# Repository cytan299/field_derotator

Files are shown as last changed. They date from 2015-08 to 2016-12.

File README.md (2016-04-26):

# A Field DeRotator for Alt-Az Mounted Telescopes Used for Astrophotography

by C.Y. Tan 2015

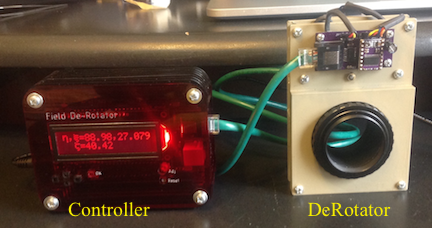
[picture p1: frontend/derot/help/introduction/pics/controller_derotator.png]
Field DeRotator


Most telescopes used for astrophotography are equatorially
mounted. However, the more popular computer controlled telescopes are
alt-az mounted and are usually deemed unsuitable for
astrophotography. The reason is that alt-az mounted telescopes have
one more degree of freedom that is not corrected because it does not
affect visual observations of celestial objects. Unfortunately, by
leaving it uncorrected, alt-az telescopes cannot be used for long
exposure astrophotography. In order to overcome this flaw in alt-az
mounted telescopes, I have designed and built a field derotator that
removes this degree of freedom and thus allows alt-az telescopes to
become astrophotography platforms.

## Goal

I have built a fully functional field derotator that consists of both
a mechanical derotator and an Arduino based controller for the
LX200. All hardware, drawings, schematics, software and documentation
are open source with the respective licenses described below.

I hope that this device will be useful for astrophotographers who find
polar mounts a real pain in the rear to use, and prefer alt-az mounts
instead.

## IMPORTANT!

Field derotation **cannot** work without an off-axis guider. If you
don't plan on investing in an off-axis guider, don't bother building
this device because field derotation will not work without it.  See
[field_derotator_formula.pdf](field_derotator_formula/field_derotator_formula.pdf)
for the explanation.

## MAC OS X Frontend Executable

A compiled app bundle for the Mac can be downloaded from the
[releases repository](https://github.com/cytan299/field_derotator/releases).

## Support

All the software have been successfully compiled on Mac OS X 10.10.5
(Yosemite).

I don't do Windows or Linux so, I cannot answer questions for these
two platforms.

This is unsupported software and hardware. Build at your own peril! :)

You can submit questions or bug reports using the
[issues](https://github.com/cytan299/field_derotator/issues) tab on
the right and then click on **NEW**.

Have fun!

## Directory structure

* **arduino** The C++ code for the arduino MEGA2560.
* **arduino_case** The case design for the field derotator controller.
* **bom** Bill of materials for 1 field derotator. I also show the
  cost for building one.
* **eagle** Eagle schematic and board files.
* **emachineshop** eMachineshop files for the derotator aluminium
shell.
* **field_derotator_formula** derivation of the derotation formula,
  analysis of how off-axis guiding is improved with derotation and
  limitation of derotation.
* **frontend** C++ code for the GUI frontend for the user to control
the derotator.
* **howto** Guides for how to assemble the derotator and the
controller.

## Other information

More information can be found in he *README.md* files in each
directory and the
[wiki](https://github.com/cytan299/field_derotator/wiki/A-Field-DeRotator-for-Alt-Az-Telescopes-Used-for-Astrophotography)
of this project on github.

## Publications

This project has been published in
[Circuit Cellar Ink](http://www.circuitcellar.com) Issues 309 (April
2016) and 310 (May 2016), titled "A Field DeRotator for
Astrophotography by C.Y. Tan" Parts 1 and 2. Details of the motivation
for building the field derotator can be found in Issue 309 and the
description of the electronic circuits, and gear ratio calculations
can be found in Issue 310.

## Copyright
All the software, documentation, hardware that I have written is
copyright 2015 C.Y. Tan.

All software is released under GPLv3

All documentation is released under Creative Commons
Attribution-ShareAlike 3.0 Unported License or GNU Free
Documentation License, Version 1.3

All hardware is released under CERN Hardware Open License v1.2

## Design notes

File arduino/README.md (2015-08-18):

# Arduino source code

This directory contains the arduino source code for the MEGA2560. The
code has been successfully compiled using ARDUINO 1.6.4.

## Directories

* **derot** This contains the *derot.ino* file which is the entry point
for the controller program.
* **lib** This contains the libraries which are required for compiling
  *derot.ino*. The README.md file contains more information about
  these libraries.

## Copyright

The software that is written by the author is copyright 2015 C.Y. Tan
and released under GPLv3.

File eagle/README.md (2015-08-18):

# Eagle files

These are the eagle files that can be sent to pc board manufacturers to
be made. There is a free version of [eagle](http://cadsoftusa.com)
that can be downloaded to view the designs.

## Directories

* **driver_module** The driver module is mounted on the derotator that
  takes signals from the controller to step the stepper motor. It also
  sends back an interrupt signal when the derotator is at its *HOME*
  position.
* **field_rotator** This is the module that is installed in the
  Arduino controller that acts as the interface between the MEGA2560
  and the LX200 and the driver_module.

## Copyright

The schematic and board designs are copyright 2015 C.Y. Tan and
released under the CERN Open Hardware License v1.2

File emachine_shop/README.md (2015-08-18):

# eMachineShop files

These files are to be sent to
[eMachineshop](http://www.emachineshop.com) to be manufactured. These
files can be read and modified using the free eMachineshop cad
software.

## Files
* **Camera_Hub_v2.ems** the hub that holds the camera.
* **Telescope_cover1_v2.ems** the cover on the side that faces the
telescope.
* **camera_cover1_v2.ems** the cover on the side that faces the
camera.

## Copyright

These mechanical designs are copyright 2015 C.Y. Tan and
released under the CERN Open Hardware License v1.2

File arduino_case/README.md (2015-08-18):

# Arduino case

This is the case that I designed for the controller. This design is based on the [slicecase](http://www.slicecase.com) style of cases. Unfortunately, it seems that slicecase is no longer in business.

The file *ponoko_upload.svg* file can be uploaded to [Ponoko](http://www.ponoko.com) for manufacture. The material that I used is

* Acrylic - Red TINT
* 3.0 mm thick
* P2 - 384.0 mm long x 384.0 mm wide

## Copyright

The case design is copyright 2015 C.Y. Tan and released under the CERN Open Hardware License v1.2

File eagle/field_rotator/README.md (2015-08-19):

# Field Rotator Controller

This is the module that is installed in the Arduino controller that
acts as the interface between the MEGA2560 and the LX200 and the
driver_module.

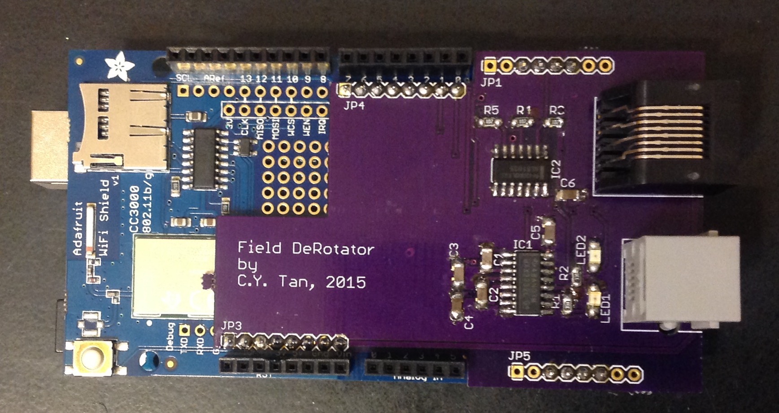
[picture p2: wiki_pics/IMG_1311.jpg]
Field Rotator Controller Module


## Copyright

The schematic and board designs are copyright 2015 C.Y. Tan and
released under the CERN Open Hardware License v1.2

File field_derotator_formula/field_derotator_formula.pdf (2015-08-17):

### An Analysis Of Field De-rotation For Alt-Az Mounted Telescopes

C.Y. Tan∗

This document is released under the

Creative Commons Attribution-ShareAlike 3.0 Unported License

BY:

(Dated: August 1, 2015)

### Abstract

A field de-rotator is mounted on an alt-az telescope in order to compensate for the field rotation

of the stars while the telescope is tracking the horizontal and vertical motions of one star (called

the “track star”) with the alt-az method. However, alt-az tracking of the track star is not perfect

and thus corrections to these errors must be made with a guiding program. The only guiding

choice that is compatible with field de-rotation is the off-axis guiding method. Unfortunately,

off-axis guiding, like its name implies, can never use as the guide star, even if available, that is

at the optical axis of the telescope, which also serves as the motor axis of the de-rotator. To

the casual observer, it would seem that de-rotation would always introduce a guide error because

of the mismatch between reference stars for the two systems. But, in fact, de-rotation coupled

with alt-az tracking actually reduces the alt-az guide error! This reduction in guide error does not

persist indefinitely because as the camera rotates, the initial guide axes used by the alt-az guiding

program will rotate away from their initial directions and thus at some point, the guide axes will

have rotated so far from their initial directions that off-axis guiding will fail. Thus, the loss of axes

integrity that comes from field de-rotation naturally introduces a time integration limit. The goals

of this paper are (a) to derive the formula for the rate of de-rotation when only alt-az tracking is

used, (b) demonstrate the reduction in guide error when both de-rotation and alt-az tracking are

used together, and (c) to calculate the integration time limit that arises from the loss of guide axes

integrity.

∗
cytan299@yahoo.com

I. INTRODUCTION

It is well-known that an alt-az mounted telescope cannot be used for astrophotography

because alt-az tracking only takes care of the horizontal and vertical positions of the track

star as it moves in the sky but does not take care of the rotation of other stars about the

track star. For example, Fig. 1 shows the view through a telescope of Orion when the

middle star of Orion’s belt, Alnilam, is alt-az tracked. And despite, Alnilam being pefectly

tracked in all the frames, Orion rotates about Alnilam. This effect is more dramatically

demonstrated in Fig. 2 where I have stacked all 12 frames shown in Fig. 1 on top of each

other.

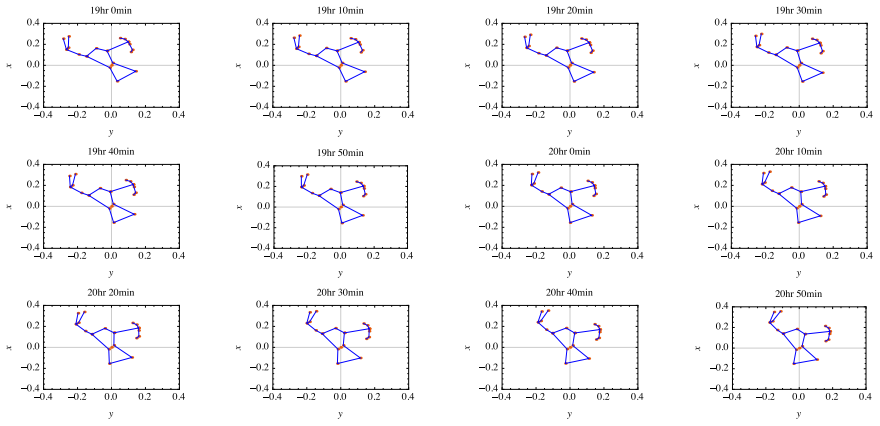
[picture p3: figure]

FIG. 1. These 12 frames represent the view of Orion seen through a telescope that is alt-az mounted

in Chicago, on 24 Jan 2015 from 1900 hours to 2050 hours in 10 minute intervals. Alnilam, the

middle star of Orion, is perfectly tracked in all these frames. And despite Alnilam being perfectly

tracked, all the other stars of Orion rotate about it. Note: I have swapped the traditional directions

of the x and y axis here because of the way I have named other vectors later in this paper.

Thus, there is a rotational degree of freedom that alt-az tracking does not correct. The

traditional ways to take care of this effect are:

(a) Abandon the alt-az mount and use an equatorial mount.
(b) Add a field de-rotator to the alt-az mount to counter the field rotation.

Due to the limitations of both where I can mount my telescope to see Polaris in my

yard and the obstruction of the telescope when my camera is mounted to do a proper Polar

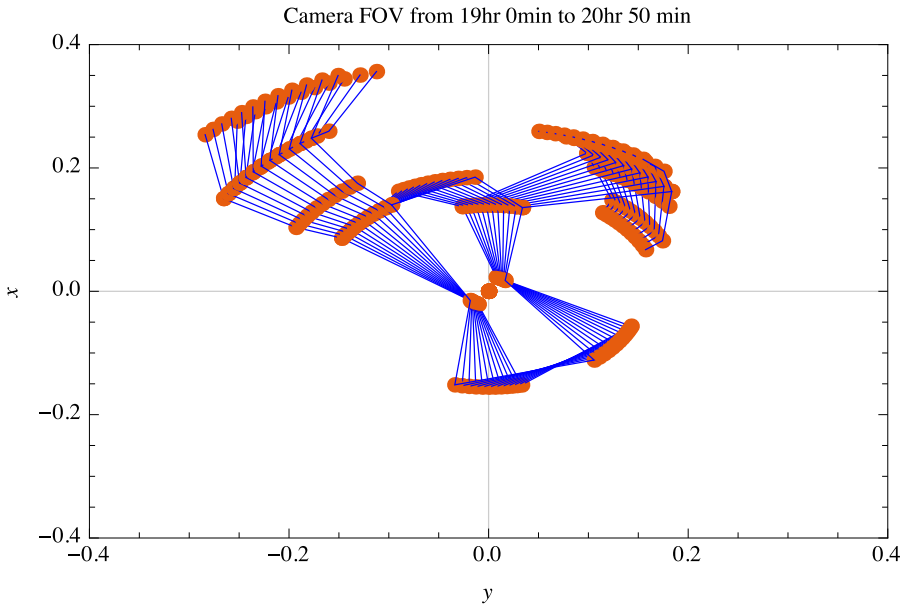
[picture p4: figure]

FIG. 2. The frames shown in Fig. 1 are stacked and the effect of rotating about Alnilam is more

obvious.

alignment, the only method open to me is to use a field de-rotator in the alt-az mount

configuration with an off-axis guider.[1] However, it is not clear to me that a field de-rotator

would actually work properly because I suspect that there are limitations that have not been

published widely. Therefore, the goal of this paper is to explore how well this technique works

(or does not) for the astrophotography community and myself.

A. Nomenclature

I define both “track star” and “guide star” here in order to avoid any confusion later in

the paper about which star I am talking about.

(a) track star The star that is being tracked by the telescope’s alt-az motors and is at the

optical axis of the telescope. This is usually the star that the user punches into the

“goto” system of the telescope so that it shows up at the centre of the field of view.

Tracking does not involve a feedback loop, i.e. it runs open loop.

(b) guide star The star that is used as a reference star by a software program that commands

the alt-az motors to rotate the telescope in such a manner as to keep this star at a fixed location in the field of view of the telescope. Guiding involves a feedback loop. It is

unnecessary for the guide star to be the same as the track star. In fact, for off-axis

guiding, this is never the case.

II. ALT-AZ COORDINATES

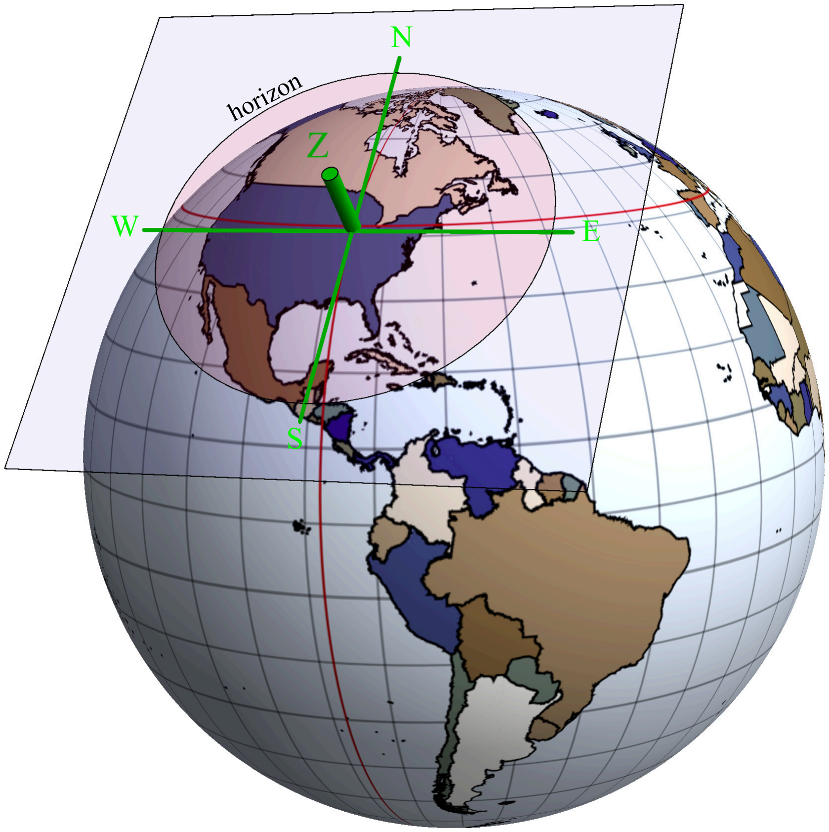
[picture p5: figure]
horizon

FIG. 3. The alt-az coordinate system starts with the construction of a tangential plane on the

Earth’s surface at the observer’s location. A horizon is defined to be a circle that is in this plane

centred at the observer. The North (N), South (S), East (E) and West (W) cardinal points are

defined to be the the intersections of these directions with the horizon. The zenith (Z) is the vector

that is normal to the horizon.

I have to explain how the alt-az system defines the coordinates of stars before we can

continue with calculating the rate of field rotation of stars even when the telescope is guided.

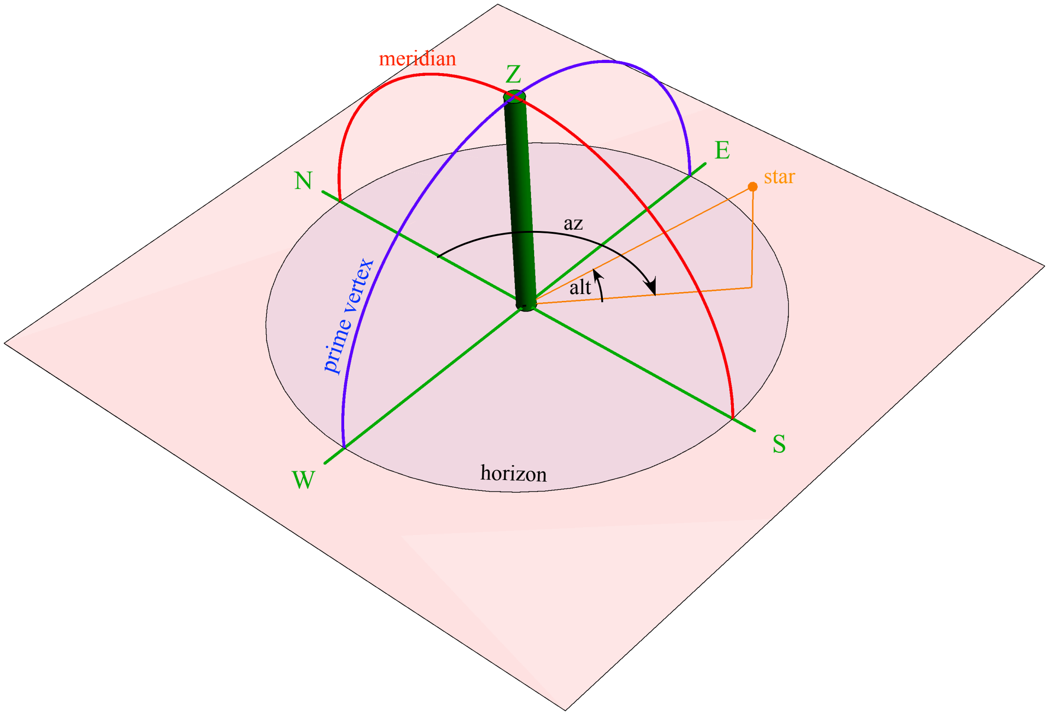
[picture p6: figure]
horizon; star; alt; meridian; prime vertex

FIG. 4. The tangential plane from Fig. 3 is transferred to this figure here. The alt-az of a star is

shown here. Its azimuth is measured clockwise from the North with North being defined as az = 0◦ .

Its alt is measured w.r.t. the horizon with the horizon being defined as alt = 0◦
. The zenith is the

point that is directly over the head of the observer. The meridian is the circle that passes through

North and the zenith. The prime vertex is the circle that is orthogonal to the meridian.

The alt-az coordinate system is the system that is based on the observer’s horizon.[2]

The horizon is defined to be the circle that lies on the tangential plane of the Earth’s sphere

at the observer’s location. This plane contains the cardinal directions north, south, east

and west and the intersection of the horizon with these directions are the points North (N),

South (S), East (E) and West (W). See Fig. 3. The meridian is defined to be the circle that

passes through the zenith and N. The NS line that is formed by intersecting the meridian

and the horizon points exactly in the north-south direction. The prime vertical is defined

to be the circle that is orthogonal the meridian. In a similar fashion, the EW line that is

formed by intersecting the prime vertical and the horizon points exactly in the east-west

direction. The alt (altitude, denoted as “η”) coordinate is the angle w.r.t. the horizon and

az (azimuth, denoted as “ξ”) is the angle w.r.t. to the NS line in the clockwise direction.

In this system, the stars do not have a fixed coordinate in alt-az because they are rotating

about Polar the axis — the axis that extends from the centre of the Earth to Polaris —

to first order. This shows up to the observer as stars rising in the East and setting in the

West. Fig. 4 shows the alt-az system. Furthermore, the alt-az coordinate of any star is

dependent on the location of the observer, i.e. their latitude and longitude, and the time the

observation is made.

III. TRACKING AND FIELD ROTATION

When I point my telescope at the star at alt-az coordinates (η0, ξ0), the star will move

away from where I’m pointing the telescope because the Earth is rotating. In order, to keep

the telescope pointed at the star, the telescope will need to track the Earth’s rotation. This

is usually accomplished with the tracking electronics that comes with the telescope’s “goto”

system. Suppose I choose a star S0 to observe, the tracking system should, in principle, keep

this star at the centre of its field of view (FOV). Note that S0 is not necessarily the star

that is used for guiding. In fact, for off-axis guding, this star is never at the centre, it is at

one edge of the FOV. And because S0 is the track star, with perfect tracking, it will always

remain at the centre of the FOV of the telescope.

As had been explained in the Introduction, stars that are not S0 will rotate about it at

some angular frequency. The goal of this section is to calculate this frequency.

A. Establishing the coordinate systems

The system that I want to solve for is shown in Fig. 5 and this system was constructed

to fulfill the following criteria:

(i) The FOV of the camera that is attached to the telescope sees a very small angular

patch of the sky. Therefore, I can approximate the camera’s FOV as a tangential plane

that is normal to the vector S0.

(ii) I can establish a Cartesion coordinate system, ˆxyẑˆ, that has its origin fixed on S0. I

will set up the ˆxyẑˆ system so that as S0 and all the stars move across the sky, the

alt-az tracking electronics of the telescope keeps the origin of the ˆxyẑˆ axes fixed on S0.

(iii) Finally, let me choose another star S1 that has alt-az coordinates (η1, ξ1) and is within

the FOV of the camera. Since S0 and S1 are within the same small FOV of the camera, I

can make the approximation that S1 which lies on the celestial sphere, can be projected

onto the tangential plane defined by S0 that has coordinate axes ˆxyˆ shown in Fig. 5.

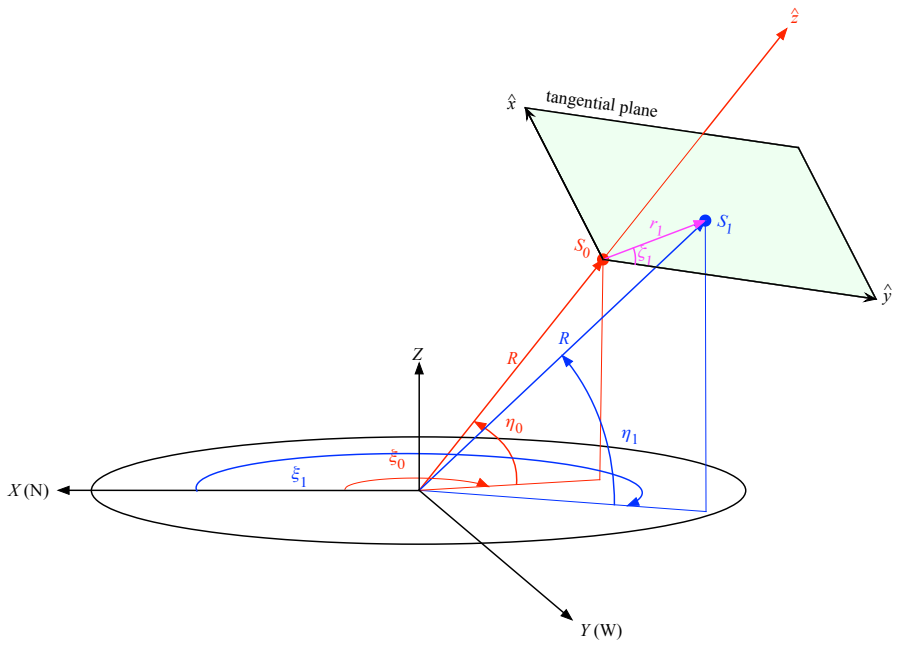
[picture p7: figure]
tangential plane

FIG. 5. The alt-az coordinates of the track star S0 and some other star S1 as seen on the tangential

plane. A small patch on the tangential plane serves as the FOV of the camera. The angle ζ1 is the

angle of interest that I need to find in order to calculate the field rotation rate ˙ζ1.

1. The alt-az system as a Cartesian coordinate system

I can write down the coordinates of any star in terms of a Cartesian coordinate system

XY Z that has the X axis pointing to the North, the Y axis pointing to the West and Z

pointing overhead. This system is shown in Fig. 5. It is clear that the XY Z coordinate

system that I have defined is consistent with the alt-az coordinate system.

The Cartesian coordinates of S0 are

S0 =

X0

Y0

Z0

=

R cos η0 cos ξ0

−R cos η0 sin ξ0

R sin η0

(1)

where R is the radial distance to any star on the Celestial sphere. In general, all the quantities

that interest us will eventually be independent of R because they deal with angles.

And similarly, I can write down the Cartesian coordinates of S1 and they are

S1 =

X1

Y1

Z1

=

R cos η1 cos ξ1

−R cos η1 sin ξ1

R sin η1

(2)
2. xŷẑˆ system

Next, I want to construct the orthornormal vectors that define the ˆxyẑˆ system. In this

system, the origin of this system is always fixed on S0 because the telescope is perfectly

alt-az tracked. The tangential plane shown in Fig. 5 is defined by the vector S0 because it

is normal to it. Let me write down the unit vector zˆ that is parallel to S0

zˆ =

1
p
X²
0 + Y

2
0 + Z

2
0

X0

Y0

Z0

(3)

And without any loss of generality, I can create yˆ that is parallel to the horizontal plane,

i.e. normal to Z. In order to make sure that yˆ is in the tangential plane, I require that yˆ

be normal to zˆ. I can summarize these requirements mathematically below

yˆ · zˆ =

yX

yY

yZ

·

X0

Y0

Z0

= 0 | (4)

yˆ · Z =

yX

yY

yZ

·

0

0

1

= 0 | (5)
|yˆ| = 1 | (6)

The above is easily solved and gives me

yˆ =

yX

yY

yZ

=

√

Y0
X²
0 +Y

2
0
−√

X0
X²
0 +Y

2
0
0

(7)

Finally xˆ is found by taking the cross product between yˆ and zˆ

xˆ = yˆ × zˆ =

1
p
(X²
0 + Y

2/0)(X²
0 + Y

2
0 + Z

2/0)

−X0Z0

−Y0Z0

X²
0 + Y

2
0

(8)
B. The initial angle ζ1

I want to calculate the angle ζ1 that is between the star S1 and the yˆ axis shown in Fig. 5.

In order to find this angle, I have to find the coordinates of r1 in the ˆxyẑˆ system. But first,

in the XY Z coordinate system, r1 has the following coordinates

r1 = S1 − S0 =

X1 − X0

Y1 − Y0

Z1 − Z0

(9)

The matrix R˜ that transforms the coordinates any vector in the XY Z system to the ˆxyẑˆ

system is

R˜ =

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
X0Z0
(X²
0 +Y

2/0)(X²
0 +Y

2

0 +Z²
0

)

−√

Y0Z0
(X²
0 +Y

2/0)(X²
0 +Y

2

0 +Z²
0

)

√
X²
0 +Y

2
√ 0
X²
0 +Y

2

0 +Z²
0
√

Y0
X²
0 +Y

2
0

−√

X0
X²
0 +Y

2
0

0
√

X0
X²
0 +Y

2

0 +Z²
0

√

Y0
X²
0 +Y

2

0 +Z²
0

√

Z0
X²
0 +Y

2

0 +Z²
0

(10)

Using the above matrix, I can calculate r1’s coordinates in the ˆxyẑˆ system. I will denote

the r1 vector in the ˆxyẑˆ system as r

0
1

r

0

1 = Rr˜
1 =

−X0X1Z0+X²
√ 0Z1+Y0(−Y1Z0+Y0Z1)
(X²
0 +Y

2/0)(X²
0 +Y

2

0 +Z²
0

)

X

√1X0−X0Y1
X²
0 +Y

2
0
−X²
0 +X0X1−Y

2
√ 0 +Y0Y1+Z0(−Z0+Z1)
X²
0 +Y

2

0 +Z²
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
(11)

Therefore, the angle ζ1 is given by

tan ζ1 =

r

0
1ˆx
r

0
1ŷ

=

−X0X1Z0 + X²
0Z1 + Y0(−Y1Z0 + Y0Z1)
(X1Y0 − X0Y1)

p
X²
0 + Y

0 + Z

(12)

1. The effect from the rotation of the Earth

The stars in the sky do not stay still. They rotate about the Polar axis by an angular

velocity Ω and the angular changes of the stars can be found by using a rotation matrix

about the Polar axis. See Fig. 6. It is obvious from this figure that the Polar axis of rotation

has the alt-az coordinates (ηP , ξP ) = (φlat, 0). I can write down its Cartesian coordinates as

SP =

XP

YP

ZP

=

cos φlat

0

sin φlat

(13)

The rotation matrix Ũ
P about SP is

Ũ
P (θ) =

cos² φlat + sin² φlat cos θ − sin φlat sin θ (1 − cos θ) cos φlat sin φlat

sin φlat sin θ | cos θ | − cos φlat sin θ
(1 − cos θ) cos φlat sin φlat | cos φlat sin θ | sin² φlat + cos² φlat cos θ

(14)

where θ is the angle of rotation.

For us, θ = Ωδt where δt is the time that has elapsed after observing the star at S0 and Ω is the Earth’s angular velocity. With the rotation matrix Ũ
p, I can calculate the position of any arbitrary star S at time δt. With no loss of generality, let me apply Ũ
P to our track

star S0. At time δt, its position becomes

S0(δt) = Ũ
P (Ωδt)S0

=

cos φlat(X0 cos φlat + Z0 sin φlat)(1 − cos Ωδt) + X0 cos Ωδt − Y0 sin φlat sin Ωδt

Y0 cos Ωδt + (X0 sin φlat − Z0 cos φlat) sin Ωδt

sin φlat(X0 cos φlat + Z0 sin φlat)(1 − cos Ωδt) + Z0 cos Ωδt + Y0 cos φlat sin Ωδt

≈ S0(0) + Ωδt

−Y0 sin φlat

X0 sin φlat − Z0 cos φlat

Y0 cos φlat

if Ωδt 1 | (15)

And to obtain S1(δt), I simply replace the subscript 0 with 1 in the above equation.

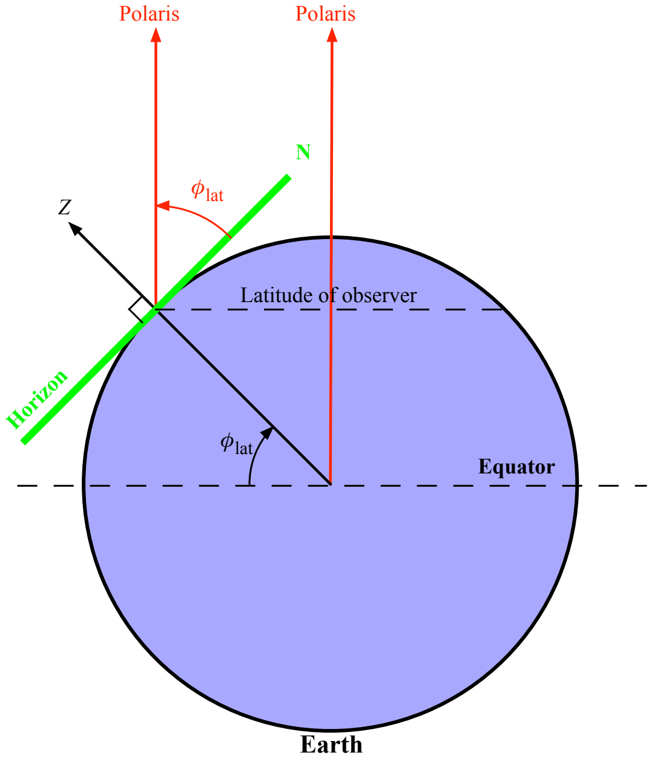
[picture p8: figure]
Polaris; φlat; Equator; Earth; Horizon; Latitude of observer
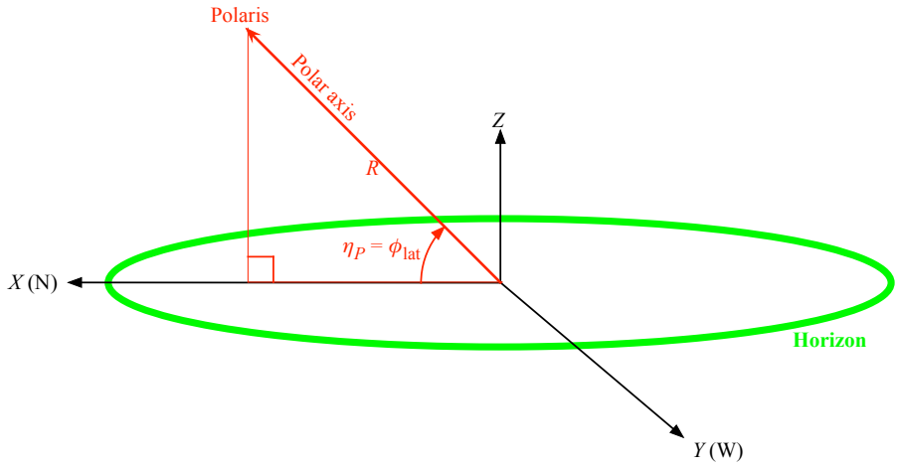
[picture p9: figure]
ηP = φlat; Polaris; Horizon; Polar axis

FIG. 6. For our purposes, the Earth’s rotation axis essentially points at Polaris which I will call

the Polar axis. The altitude angle of the Polar axis has the same angle as the observer’s latitude,

i.e. ηP = φlat, and its azimuth angle ξP = 0 by definition.

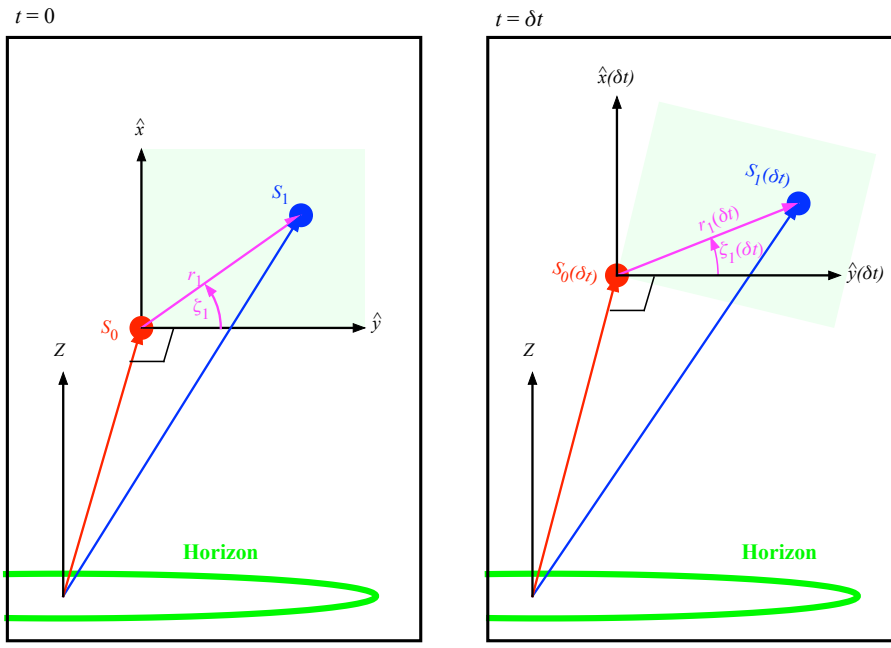
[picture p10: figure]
Horizon
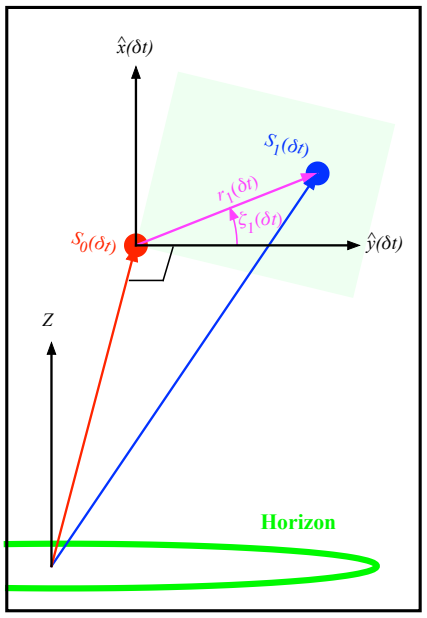
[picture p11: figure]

FIG. 7. At t = 0, the r1 vector and the yˆ vector encloses the angle of interest ζ1. The light green

rectangle represents the FOV at t = 0. At time t = δt, the stars have rotated and the original

FOV (light green rectangle) has rotated by the same amount despite the alt-az tracking mechanism

having moved the telescope so that S0 is still at the same point in the new FOV defined by xˆ and

yˆ. Notice that the mechanics of alt-az tracking always keeps yˆ parallel to the horizontal plane

and normal to S0. The difference ζ1(δt) − ζ1(0) tells us how much the stars have rotated w.r.t. S0

during the time interval δt.

It is clear from Fig. 7 that the vector r1(δt) is given by

r1(δt) = S1(δt) − S0(δt)

= S1(0) − S0(0) + Ωδt

−(Y1 − Y0) sin φlat

(X1 − X0) sin φlat − (Z1 − Z0) cos φlat

(Y1 − Y0) cos φlat

(16)

where I have applied Eq. 15.

In a similar vein, I must also rotate the tangential plane with coordinate system defined

by S0 to S0(δt). This is exactly what alt-az tracking does, it moves the telescope so that S0

is always at the centre of its FOV. Since the tangential plane has moved, I have to create

a new ˆxyẑˆ(δt) coordinate system with the same method that I had used in section III A 2.

From these new vectors, I can construct the transformation R˜(δt) matrix that takes vectors

from the XY Z coordinate system to the ˆxyẑˆ(δt) system and it is

R˜(δt) =

xˆ

T
(δt)

yˆ

T
(δt)

zˆ

T
(δt)

(17)

Unfortunately, writing out R˜(δt) is rather onerous and not very illuminating. But after a lot

of algebra, once I have R˜(δt), I can transform r1(δt) that is in XY Z coordinates to ˆxyẑˆ(δt)

coordinates

r

0/1(δt) = R˜(δt)r1(δt)

= R˜(δt)r1(0) + ΩδtR˜

−(Y1 − Y0) sin φlat

(X1 − X0) sin φlat − (Z1 − Z0) cos φlat

(Y1 − Y0) cos φlat

≡

r

0
1ˆx

(δt)

r

0
1ŷ

(δt)

r

0
1ẑ

(δt)

(18)

And by using Eq. 12 and the above equation for r

0/1(δt), I can calculate the new angle ζ1(δt)

and the result is
tan[ζ1(δt)] = r

0
1ˆx

(δt)
r

0
1ŷ

(δt)

(19)

C. Field rotation frequency ˙ζ1

Finally, I can calculate the field rotation frequency ˙ζ1. To do this, let me define δζ1 to be

the difference ζ1 at t = 0 and t = δt, i.e.

| δζ1 = ζ1(δt) − ζ1(0) | (20)

In order to apply Eq. 12 and 19 to get the ˙ζ1, I have to take the tangent of δζ1. This gives

me

tan(δζ1) = tan[ζ1(δt) − ζ1(0)] = tan[ζ1(δt)] − tan[ζ1(0)] 1 + tan[ζ1(δt)] tan[ζ1(0)]

≈ δζ1 | if δζ1 1. | (21)

where the last line in the above equation is a consequence of Ωδt 1.

Recall that Eq. 21 is the result in Cartesian XY Z coordinates. What I really want is the

result in alt-az coordinates which I can get when I substitute Eq. 1 and 2 into Eq. 21. After

I do this, I get a very simple solution for δζ1 which is

δζ1 = −Ωδtcos ξ0 cos φlat
cos η0

(22)

It is important to notice that δζ1 does not have any dependence on R or the choice of the

non-tracked star S1. This makes sense because otherwise the relative positions of the stars,

for example constellations, as seen by the camera will become distorted as the stars rotate

about the Polar axis.
The result that I have been hunting for, the field rotation frequency ˙ζ1, can be read off

immediately from Eq. 22 and is

˙ζ1 = lim

δt→0

δζ1
δt = −Ω

cos ξ0 cos φlat
cos η0
≡ ˙ζ | (23)

And from this equation, it is obvious that ˙ζ1 is independent of the choice of star S1 and thus

I have removed the subscript “1” from ζ1 and will just call it ζ from now on.

Note: the Earth’s angular rotation frequency is Ω = −[(4.178 × 10⁻³ | ) × π/180] rad/s.

The negative sign comes from making sure that the stars rise from the East and sets in

the West because when I apply the right hand rule about the Polar axis, a positive angular

frequency means that the stars rise in the West and sets in the East.

1. Speed Limit

It is clear that ˙ζ has a singularity when the telescope points towards the zenith, i.e. η0 =

90◦
. This also means that as the telescope gets closer and closer to the zenith, the stepper

motor must rotate faster and faster to compensate for the Earth’s rotation. This naturally

sets a maximum altitude limit that the field de-rotator can be used. For example, if the maximum stepper motor revolution frequency, ˙ζmax rad/s, is known, then the maximum

altitude ηmax that the telecope can point to is

ηmax = cos⁻¹

Ω

˙ζmax

cos ξ0 cos φlat
(24)

For example, for where I live, Chicago’s latitude is φlat = 41.8369◦ and when I choose

˙ζmax = 1 Hz = 2π rad/s for maximum stepper motor torque, I obtain ηmax = 89.9995◦

when ξ0 = 90◦

(E) or 270◦
(W). Thus, in principle, as long as I do not point the telescope

towards the zenith, the stepper motor revolution frequency is not the limiting factor. The

only other integration time limiting factor comes from the loss of guide axes integrity which

I will discuss in section IV B.

IV. OFF-AXIS GUIDING

Now, here’s the section where I start discussing the limitations that field de-rotation

introduces to off-axis guiding. I would like to remind the reader that “tracking” is distinct

from “guiding” in this paper. Their definitions have been discussed in section I A. Here are

some interesting consequences when de-rotation is added to tracking to off-axis guidng

(a) In off-axis guiding, a guide star Sg is chosen that is never at the optical axis of the

telescope. (Note: In general, the rotation axis of the de-rotation motor is at the optical

axis of the telescope.) It does seem, at first glance, that de-rotation adds to the guide

error because the two axes are not coincident. However, I will demonstrate in the

following section that, in fact, de-rotation coupled with tracking reduces guide errors.

Unfortunately, this piece of good fortune does not persist indefinitely. See next item.

(b) As the field de-rotation mechanism rotates the camera, the up-down (traditionally called

N-S) and left-right (traditionally called E-W) axes rotate away from their initial direc-

tions. At some point, the off-axis guiding software will fail because the axes have moved

too far from their initial directions. This loss of axes integrity limits the integration

time for photographing deep sky objects.

In the next subsections, I will analyze both (a) and (b).

A. Reduction of off-axis guiding error by de-rotation and tracking

I can demonstrate how the guide error is reduced to zero when a field de-rotator is added

to alt-az tracking in the ideal world. I have drawn Fig. 8 to show the view through a

telescope where there are two stars S0 and Sg. The star S0 is the track star that lies at

the centre of the FOV and Sg is the guide star that lies at some position offset from S0.

Fig. 8(a) shows what happens at t = 0 and t = δt later when only alt-az tracking is used to

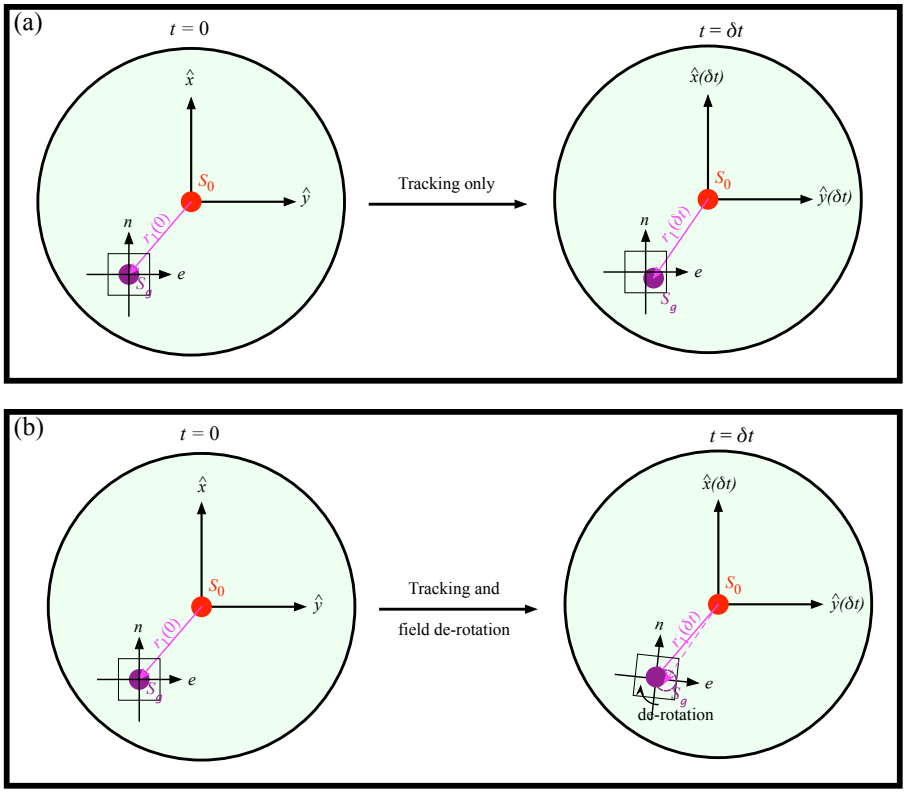
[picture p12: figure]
Tracking only; Tracking and; field de-rotation; de-rotation

FIG. 8. These are the views through a telescope where its optical axis has been aligned to S0 and a

star Sg has been chosen to be the guide star. Sg lies in the cross-hairs of the off-axis guider. If alt-az

tracking is the only method used to keep S0 centred in the FOV, (a) shows that Sg rotates away

from the off-axis cross-hairs due to field rotation that I had discussed earlier, while (b) is the case

where both tracking and field-rotation is applied. In this case, Sg remains on the cross-hairs of the

off-axis guider. Thus, de-rotation has removed any guide errors! However, notice that de-rotation

has caused the guide reference axes (n, e) to rotate from their initial directions.

keep S0 in the centre of the FOV. While S0 remains fixed at the centre of the FOV, Sg has

rotated away from the cross-hairs of the off-axis guider. However, when field de-rotation is

added to alt-az tracking, Sg remains fixed in the cross-hairs of the off-axis guider. Thus,

if both alt-az tracking and de-rotation are perfect, the off-axis guider has nothing to do!

Unfortunately, neither mechanisms are perfect in real life and therefore there will be errors

that the off-axis guider have to correct. Here is where the limitations to the integration time

comes in: de-rotation rotates the guide reference axes (e, n) shown in Fig. 8(b) away from

their original directions.

In the next subsection, I will complete the analysis of the loss of guide axes integrity.

After that, I will do an analysis of how the errors from de-rotation and alt-az tracking affect

off-axis guiding accuracy.

B. Loss of guide axes integrity

The loss of guide axes integrity is illustrated in Fig. 8(b) at t = δt where due to field

de-rotation, the formerly up-down (n), left-right (e) cross-hairs shown in the other FOV’s

have rotated so that they are no longer perfectly up-down or left-right. As time marches

on, the n and e orthogonal vectors that make up the guide axes rotate further and further

away from their initial directions and thus at some point in time, the off-axis guider cannot

cope with the change in directions of the axes n and e because the alt-axis program no

longer knows how to direct the alt-az motors to move the telescope up-down and left-right.

This loss of guide axes integrity limits the integration time that can be used to photograph

deep sky objects. In the next two section, I will calculate both the de-rotation angle and

integration time limitations.

1. De-rotation angle limit

The first thing I need to do is to define the metric that tells me how well the alt-az

tracking system performs after its original (e, n) axes rotates by an angle ζ to the new (n

0
, e

0
) axes due to the actions of the field de-rotator.

Let me suppose that the guide star Sg is no longer at the centre of the cross hairs. See

Fig. 9. The alt-az guider queries the camera to tell it where Sg is. The camera tells the

alt-az guider that Sg is at polar coordinates (ε, γ) in the (e

0
, n

0
) frame. The alt-az guider

now knows that Sg is no longer at the centre of the cross hairs and thus applies the following

correction to bring Sg back to the centre of the cross-hairs

∆e = − cos γ

∆n = −sin γ | (25)

where ∆e is the amount of correction in the e direction and ∆n is the amount of correction

in the n direction. Notice that these corrections are in the (e, n) frame because the off-axis

n

e

n'

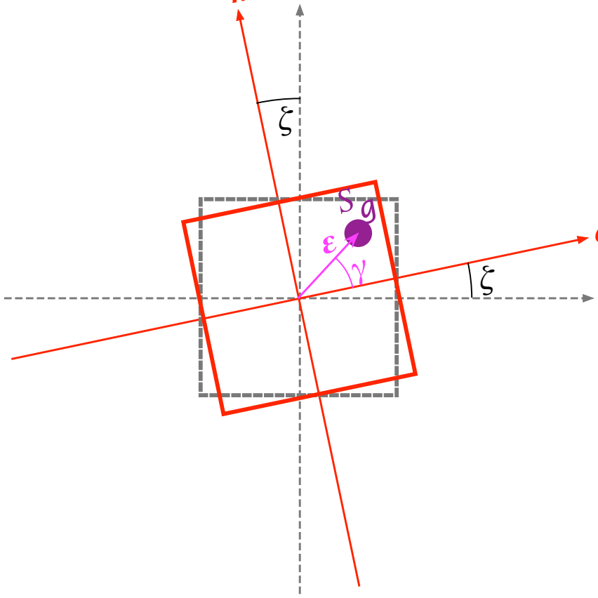
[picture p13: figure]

e'

FIG. 9. The guide reference axes (e, n) is rotated by an angle ζ to (n

0
, e

0
). The guide star Sg is

offset from the centre of the cross hairs by the polar coordinates (, γ) w.r.t. the (n

0
, e

0
) axes and

(, γ + ζ) w.r.t. the (e, n) axes.

guider program does not know that its guide axis has rotated. Thus the correction has not

completely moved Sg back to the centre of the cross hairs. In fact, the residual errors are

δe = ε[cos(γ + ζ) − cos γ]

δn = ε[sin(γ + ζ) − sin γ] | (26)

which tells me the added corrections, δe and δn, that are needed for the the alt-az guider

to bring Sg back to the centre of the cross-hairs. These two numbers allow me to create an

error radius δε

δε =

√
δe² + δn²

= ε

q
[cos(γ + ζ) − cos γ]

2 + [sin(γ + ζ) − sin γ]

2
(27)

Of course, the whole point of alt-az guiding is to require that the correction error be smaller

than the error before correction, i.e. I require δε < or else the guiding process becomes

rather pointless! This inequality means that
q
[cos(γ + ζ) − cos γ]

2 + [sin(γ + ζ) − sin γ]

| 2 < 1 | (28)

If the initial angular error γ is uniformly distributed between 0 and 2π, the probability

density function is

p(γ) =

1
2π

0 ≤ γ < 2π

0 otherwise

(29)

then the mean value[3] of δε comes from integrating Eq. 28 and is
Z ∞

−∞

dγ q
[cos(γ + ζ) − cos γ]
2 + [sin(γ + ζ) − sin γ] | 2 p(γ) <

Z ∞

| −∞

dγ [1 × p(γ)]

p
2(1 − cos ζ) < 1
⇒ | cos ζ > 1/2 | (30)

and thus |ζ| < π/3 or 60◦
. This is a surprisingly large number that is independent of camera

pixel size, focal length of the telescope etc. It only depends on how much the camera has

rotated away from its initial position. How long the camera takes to rotate by 60◦
| | is in turn

dependent on which star the telescope is pointing at. In the next section, I will calculate the

maximum integration time for every point on the celestial sphere using this rotation angle

limit.

C. Maximum integration time

The maximum integration time tmax is limited by the result from the previous section

|ζ| =

Ω cos φlat Z tmax

0

dt cos ξ(t)
cos η(t)
< π/3 | (31)

and from Eq. 23 with ξ(0) = ξ0 and η(0) = η0.

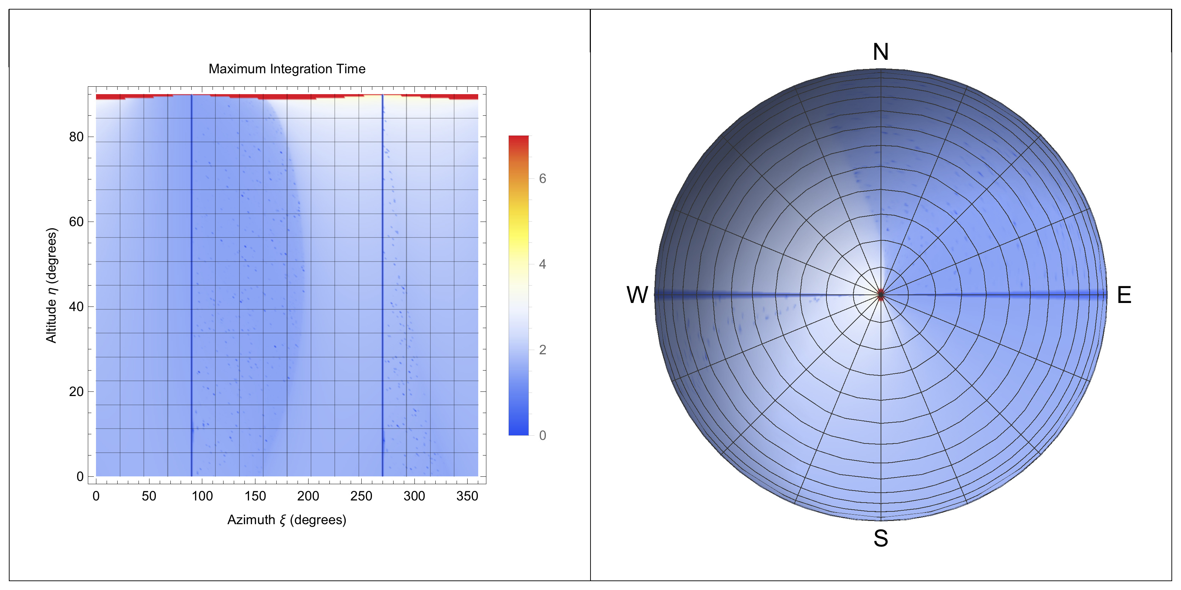
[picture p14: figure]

FIG. 10. The maximum integration time for each alt-az coordinate is plotted as a density plot as

a projection onto a Cartesian coordinate system (left) and onto a hemisphere (right) as seen from

the zenith. The integration times have been normalized by the function − log10(tmax/10⁶
) in these

plots where 10⁶
s has been used to represent infinite integration time. The longest integration time

(value 0) is coloured blue while shortest is coloured red (value 7). As expected, as the telescope

approaches the zenith η = 90◦
, the allowed integration time gets very short because the de-rotation

frequency ˙ζ → ∞.

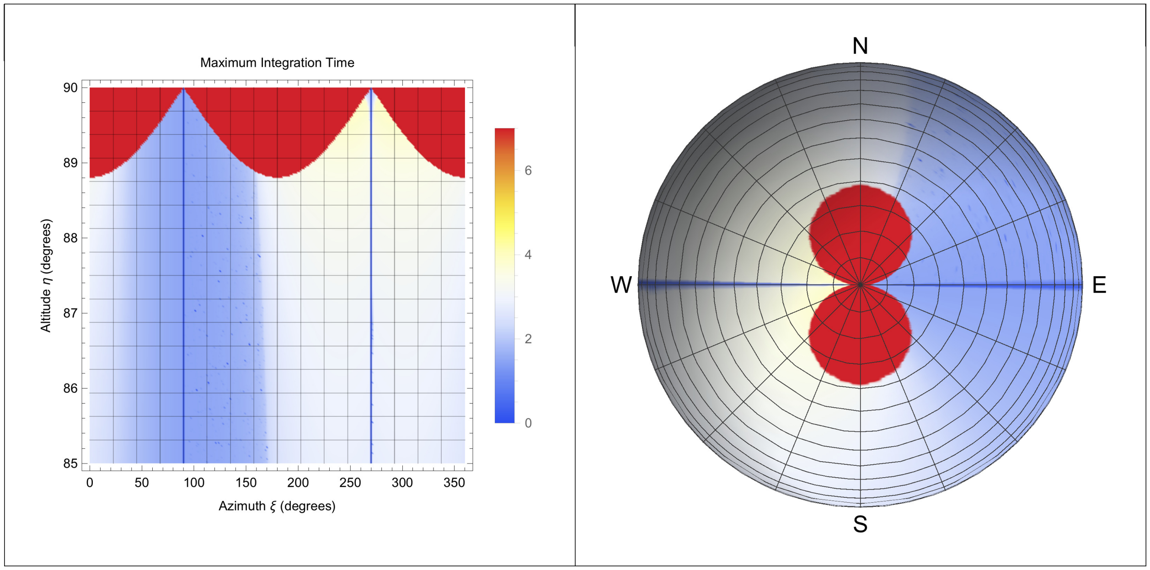
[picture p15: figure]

FIG. 11. Zoomed in view from η = 85◦

to 90◦ of Fig. 10.

From Eq. 1, I can write cos ξ and cos η in Cartesian coordinates as

tan ξ = −

Y
X

⇒ cos ξ =

X
√
X² + Y

2

tan η =

Z
X

cos ξ =

Z
√
X² + Y

2

⇒ cos η =

r
X² + Y

2
X² + Y

2 + Z²

(32)

Using the above results, I have

cos ξ
cos η

=

X

√
X² + Y

2 + Z²
X² + Y

2

(33)

and to see an explicit dependence on t on the rhs of the above, I can use Eq. 15 to get the

equations to substitute into the rhs. These equations are:

X(t) = cos φlat(X0 cos φlat + Z0 sin φlat)(1 − cos Ωt) + X0 cos Ωt − Y0 sin φlat sin Ωt

Y (t) = Y0 cos Ωt + (X0 sin φlat − Z0 cos φlat) sin Ωt

Z(t)

2 = R

2 − X(t)

2 − Y (t)

2
(34)

and Eq. 1 to write Eq. 33 in terms of the initial alt-az coordinates (η0, ξ0,) of the star.

1. Numerical solution

I can obtain an analytic solution of ζ by integrating Eq. 31 after I have substituted in

Eq. 33 and 34 into it. However, this solution is not very illuminating because it is quite

complicated. Rather than wade through this algebraic morass, I will, instead, generate an

example of the maximum integration time for every point on the celestial sphere at my

Chicago location. The results are shown in Fig. 10 and 11.

In general, from these numerical results and those from section III C 1, I have found that

as long as the telescope points between 0◦ ≤ η < 85◦
, the minimum integration time is about

24 minutes and there are no limitations that arise from the stepper motor rotation speed.

Appendix: LX200 Alt-Az coordinate system

The LX200 defines its alt-az coordinate system differently than what I have done. The 0◦

of the azimuth for the LX200 is when it points South rather than North. My investigation shows that the azimuth relationship between the azimuth of the LX200, ξLX200 and the

azimuth ξ0 discussed in this paper is:

ξLX200 = ξ0 + 180◦
(A.1)

and if the result ξLX200 > 360◦

, then ξLX200 → ξLX200 − 360◦ .

And going the other way, I have

ξ0 = ξLX200 − 180◦
(A.2)

and if the result ξ0 < 0 then ξ0 → ξ0 + 360◦
Thus, the derotation speed is related by a sign, i.e. ˙ζLX200 = − ˙ζ0 between these two

coordinate systems.

[1] The off-axis guider is needed because the alt-az guider must see the guide star in the same field

of view as the camera.

[2] The alt-az coordinate system is also called the horizonal coordinate system.
[3] A.A. Sveshnikov. Problems in probability theory, mathematical statistics and theory of random

functions, chapter IV. Dover Publications, 1968.

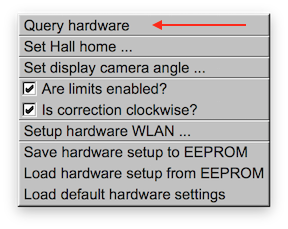
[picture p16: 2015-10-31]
frontend/derot/help/help_interface/pics/query_hardware.png

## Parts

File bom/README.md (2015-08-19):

# Bill of Materials

I present the estimated cost for building *one* field derotator here
to be $642. This is the lower bound for the cost of one such device
because, in practise, it is not possible to just buy 1 screw :) or is
cost effective to build just one part at
[eMachineshop](http://www.emachineshop.com). Plus, I did not include
tax or cost of shipping. I would imagine that if people banded
together to build multiple copies of this device, the cost will get
closer to $642.

The bom.ods file is readable using [LibreOffice Calc](http://www.libreoffice.org).

# Note

One cost that I did not include was the modification of two gears used
in this project. I had friends who were kind enough to use their lathe
and mill to perform the modifications essentially for free. See
[assembly instructions](../howto/assembly.pdf) for more information on
what modifications were made.

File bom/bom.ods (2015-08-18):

Part # | Description | Price each | # required for field rotator | Cost of 1 field rotator | Bought from | Total cost of 1 field rotator
PAAR-BP-T221 | Baader deluxe short (15 mm) SCT female to T2 male T-adapter | $60.00 | 1 | $60.00 | agenaastro.com | $642.16
S1064Z-064A200 | 64 pitch 200 teeth spur gear | $41.17 | 1 | $41.17 | Sdp-si.com (http://www.sdp-si.com/estore)
A 1B 1-Y64016 | 64 pitch 16 teeth spur gear | $2.99 | 1 | $2.99 | Sdp-si.com (http://www.sdp-si.com/estore)
1699 | Arduino Mega 2560 R3 | $44.95 | 1 | $44.95 | www.pololu.com (http://www.pololu.com/product/1699)
2773 | Adafruit wifi shield | $39.95 | 1 | $39.95 | www.pololu.com (http://www.pololu.com/product/2773)
2133 | DRV8825 stepper motor driver | $8.95 | 1 | $8.95 | www.pololu.com (http://www.pololu.com/product/2133)
2298 | Sanyo pancake stepper motor | $49.95 | 1 | $49.95 | www.pololu.com (http://www.pololu.com/product/2298)
1465 | 9V, 6A power supply | $13.45 | 1 | $13.45 | www.pololu.com (http://www.pololu.com/product/1465)
1800 | Precrimped female connectors | $0.20 | 3 | $0.60 | www.pololu.com (http://www.pololu.com/product/1800)
1981 | Nylon spacer 4 mm length | $0.04 | 4 | $0.14 | www.pololu.com (http://www.pololu.com/product/1981)
eBTC6tBG | Field rotator | $10.50 | 1 | $10.50 | www.oshpark.com (https://oshpark.com/orders/eBTC6tBG)
 | Driver module | $3.33 | 1 | $3.33
2202677 | Capacitors SMD, 0.01, 0.1 uF | $0.03 | 7 | $0.21 | www.jameco.com
524461 | Modular jack 8P8C | $0.79 | 2 | $1.58
913969 | SN74ALS1035D | $2.15 | 2 | $4.30
31114 | 47uF, 50V radial cap | $0.12 | 1 | $0.12
1996111 | LED, yellow 1206 SMD | $0.08 | 1 | $0.08
697741 | LED, green 1206 SMD | $0.10 | 2 | $0.20
698613 | MAX3232CD | $1.75 | 1 | $1.75
115837 | Modular jack 6P6C | $0.85 | 1 | $0.85
2120276 | Header, 0.1” st, male, 1row, 4pins | $0.25 | 4 | $1.00
2045350 | 0.100 low profile pins | $3.99 | 2 | $7.98 | www.jameco.com
143407 | Spacer ¼ hex aluminum | $0.59 | 4 | $2.36 | www.jameco.com
2094426 | Screw 6-32 pan head 3/8” | $0.06 | 8 | $0.47
2094397 | Screw 4-40 pan head 3/8” | $0.06 | 4 | $0.24
2202669 | smd resistors 470,3.3k,4.7k,10k,100k | $0.03 | 8 | $0.24
157383 | Connector 0.1” 3 pins | $0.29 | 1 | $0.29
100803 | Connector 0.1” 4 pins | $0.29 | 1 | $0.29
399-9362-1-ND | 4.7nF 25V SMD cap 1206 | $0.06 | 1 | $0.06
D12-N52 | 1/16” dia x 1/8” thick magnet | $0.14 | 1 | $0.14 | www.kjmagnetics.com (http://www.kjmagnetics.com/proddetail.asp?prod=D12-N52)
6809-2RS | Ball bearings 45mm ID, 58mm OD | $6.53 | 1 | $6.53 | www.amazon.com (http://www.amazon.com/WJB-6800-2RS-Series-Groove-Bearing/dp/B007HSNA6Y)
27100 | Permatex high strength threadlocker | $4.29 | 1 | $4.29 | www.amazon.com (http://www.amazon.com/gp/product/B000AAM2Z6/ref=oh_aui_detailpage_o00_s00?ie=UTF8&psc=1)
BRS-277.10 | 3/32” shank mandrel | $0.97 | 1 | $0.97 | www.amazon.com (http://www.amazon.com/gp/product/B005LI24TQ/ref=ox_sc_act_title_2?ie=UTF8&psc=1&smid=A3NUNNXXHUJDMF)
534-3487 | 6-32x0.5” aluminium standoffs | $0.38 | 6 | $2.28 | www.servocity.com (https://www.servocity.com/html/6-32_aluminum_standoffs__round.html)
L5BWDC02 | Robinson racing pinion 5mm bore 48P 17T | $8.01 | 1 | $8.01 | www.towerhobbies.com (http://www3.towerhobbies.com/cgi-bin/wti0095p?FVPROFIL=&FVSEARCH=L5BWDC02&search=Go)
L5WLJ702 | Robinson racing pinion 48 P 41T | $5.91 | 1 | $5.91 | www.towerhobbies.com (http://www3.towerhobbies.com/cgi-bin/wti0095p?FVPROFIL=&FVSEARCH=L5WLJ702)
192406 | camera cover | $62.48 | 1 | $62.48 | www.emachineshop.com
192408 | camera hub | $57.16 | 1 | $57.16
192409 | telescope cover | $64.20 | 1 | $64.20
88740006087 | M3 10mm screws | $0.16 | 2 | $0.32 | www.homedepot.com
2066188658 | Self etching primer | $4.76 | 1 | $4.76 | www.homedepot.com (http://www.homedepot.com/p/Rust-Oleum-Automotive-12-oz-Automotive-Self-Etching-Primer-Spray-Paint-249322/202097278)
2066188658 | Self etching primer | $4.76 | 1 | $4.76 | www.homedepot.com (http://www.homedepot.com/p/Rust-Oleum-Automotive-12-oz-Automotive-Self-Etching-Primer-Spray-Paint-249322/202097278)
52427603701 | Gorilla clear repair tape | $6.97 | 1 | $6.97
887480030310 | 6-32 3/4” screws+nuts | $0.15 | 4 | $0.59 | www.homedepot.com
887480035186 | M3 washer | $0.08 | 2 | $0.15 | www.homedepot.com
G3372031 | 6-32 3/4” nylon screws | $0.06 | 4 | $0.23 | www.zoro.com
G2602397 | 2-56 1/4” screw | $0.07 | 3 | $0.21 | www.zoro.com
US5881LUA | Hall effect sensor | $2.00 | 1 | $2.00 | www.adafruit.com (http://www.adafruit.com/products/158)
1490 | Tactile switch buttons 6mm tall | $0.25 | 5 | $1.25 | www.adafruit.com (http://www.adafruit.com/products/1490)
715 | Adafruit LCD shield kit | $24.95 | 1 | $24.95 | www.adafruit.com (http://www.adafruit.com/products/714)
915245 | Aluminum foil tape | $7.88 | 1 | $7.88 | www.lowes.com
57818 | 6-32 3/8” screws+nuts | $0.08 | 12 | $1.01 | www.lowes.com
62045 | 4-40 3/4” screws | $0.10 | 4 | $0.39 | www.lowes.com (http://www.lowes.com/pd_62045-37672-605392_0+1z0vixk__?productId=4746579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)
20811 | Heat shrink tubing 1/8” | $2.16 | 0 | $0.22 | www.lowes.com
136493 | 5/32*2/8*1/16 rubber washer | $0.92 | 8 | $7.36
240082 | Black chalkboard spray | $5.98 | 1 | $5.98 | www.lowes.com
351828 | Satin sagebrush spray | $5.98 | 1 | $5.98 | www.lowes.com
58121 | #6 washers | $0.03 | 8 | $0.26
102500000 | K&S 1/8” brass tubing | $1.33 | 1 | $1.33 | www.hobbylobby.com
153098 | silver leaf rub 'n buff | $5.99 | 1 | $5.99 | www.hobbylobby.com (http://shop.hobbylobby.com/products/silver-leaf-rub-n-buff-153098/)
165328 | laser cut box (red) | $46.27 | 1 | $46.27 | www.ponoko.com (http://www.ponoko.com/make/history)
161272043467 | RJ12, 6P6C reverse 14ft cable | $3.33 | 1 | $3.33 | www.ebay.com

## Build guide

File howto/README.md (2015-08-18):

# How to build the Field DeRotator

I have written these two documents to help you build and assemble a
field derotator.

## The documents

* **assembly.pdf** This guide tells you how I assembled the
  mechanical parts of the derotator. There's quite a bit to do to get
  mechanical parts painted and assembled. And glue is your friend :)
* **controller.pdf** This guide tells you how I assembled the
controller.

## Copyright

These documents are copyright 2015 C.Y. Tan and released under
Creative Commons Attribution-ShareAlike 3.0 Unported License.

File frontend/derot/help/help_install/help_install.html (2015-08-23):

# Installing the Field DeRotator

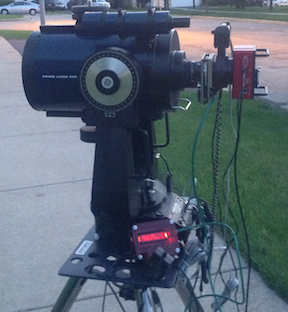
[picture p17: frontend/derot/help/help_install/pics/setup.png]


by C.Y. Tan June 2015

# Copyright

    Copyright (C)  2015 C.Y. Tan
    Permission is granted to copy, distribute and/or modify this document
    under the terms of the GNU Free Documentation License, Version 1.3
    or any later version published by the Free Software Foundation;
    with no Invariant Sections, no Front-Cover Texts, and no Back-Cover Texts.
    A copy of the license is included in the section entitled "GNU
    Free Documentation License".

# Table of Contents

- Introduction
- Nomenclature
- Installing the camera to the derotator
- Installing the derotator and camera to the telescope
- Remaining steps
- GNU Free Documentation License Notice

# Introduction

This manual describes how the user connects the derotator to both the telescope and the imaging camera.

# Nomenclature

#### Interface

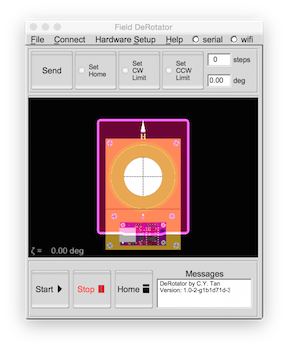
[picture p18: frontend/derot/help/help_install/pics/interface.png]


#### Controller

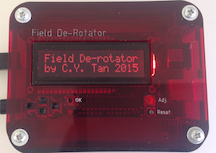
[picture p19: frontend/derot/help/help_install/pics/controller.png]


#### DeRotator

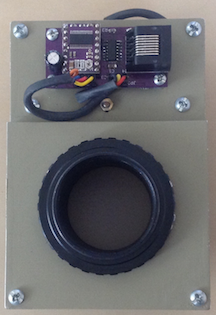
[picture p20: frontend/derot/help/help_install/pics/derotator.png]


# Installing the camera to the derotator

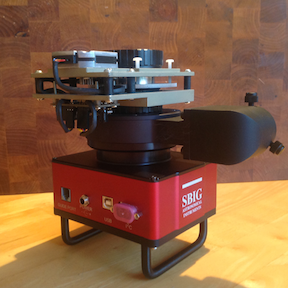
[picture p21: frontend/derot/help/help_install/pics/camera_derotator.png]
 IMPORTANT! Detach the 4-pin motor stepper motor drive cable from the derotator drive module before continuing.

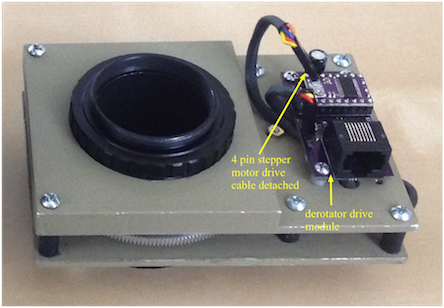
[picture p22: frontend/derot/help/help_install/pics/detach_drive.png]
The reason for disconnecting the drive cable cable is because current is generated when the drive gear is rotated and the stepper motor IC can be damaged by this current. 

This is the most tedious part of the installation that involve a number of steps.

#### Tighten the nylon screws

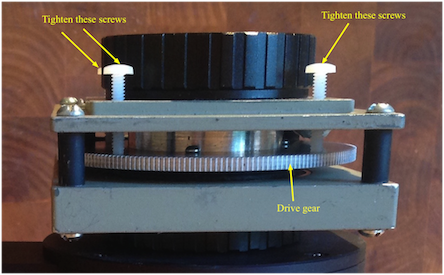
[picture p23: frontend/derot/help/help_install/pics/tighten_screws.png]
First tighten the nylon screws on the derotator so that the drive gear does not move. 

#### Catching the threads of the camera

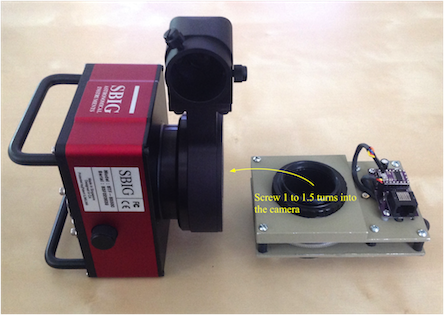
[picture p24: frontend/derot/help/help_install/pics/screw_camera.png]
With the drive gear immobilized, it is easy to get the first few turns of the male T-thread on the derotator into the camera. 

#### Screwing the derotator into the camera

For the SBIG STF-8300 camera with an off-axis guider OAG8300 attached, it is not possible to directly screw in the derotator into the camera because the off-axis guider gets in the way. The only way to screw the derotator into the camera is by

- Loosening the nylon screws so that the drive gear can move freely.
- Rotating the drive gear with your thumb until the derotator is screwed completely into the camera. See picture below.

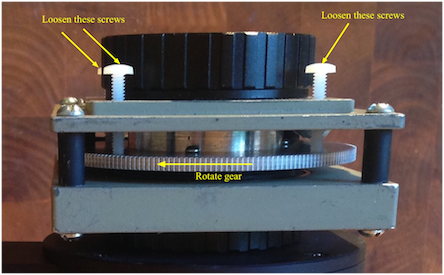
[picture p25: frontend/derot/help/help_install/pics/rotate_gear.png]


# Installing the derotator and camera to the telescope

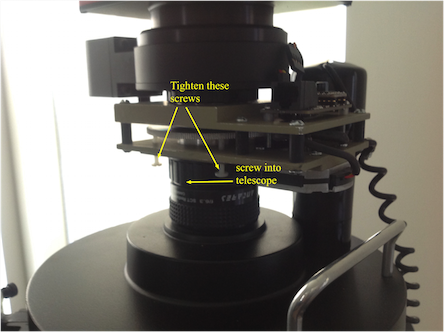
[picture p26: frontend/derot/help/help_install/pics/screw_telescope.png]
First tighten the nylon screws again and rotate the SCT female connector into the male SCT connector on the telescope.  Once the derotator and camera are attached to the telescope,

- Loosen the nylon screws
- Attach the stepper motor driver cable back to the derotator drive module.

# Remaining steps

The remaining steps involve hooking up the controller to the derotator and either using the interface to connect to the controller or operating the controller in standalone mode:

- Connecting the controller to the derotator
- Using the interface

# GNU Free Documentation License

This document is copyrighted under the GNU Free Documentation License

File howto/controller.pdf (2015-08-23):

## Controller assembly instructions

C.Y. Tan
8/22/15

2 | Field De-rotator Assembly | August 22, 2015

## License

Copyright 2015 C.Y. Tan
This document is licensed under Creative Commons Attribution-ShareAlike 3.0 Unported License. To view a copy of this license, visit http://creativecommons.org/licenses/by-sa/3.0/

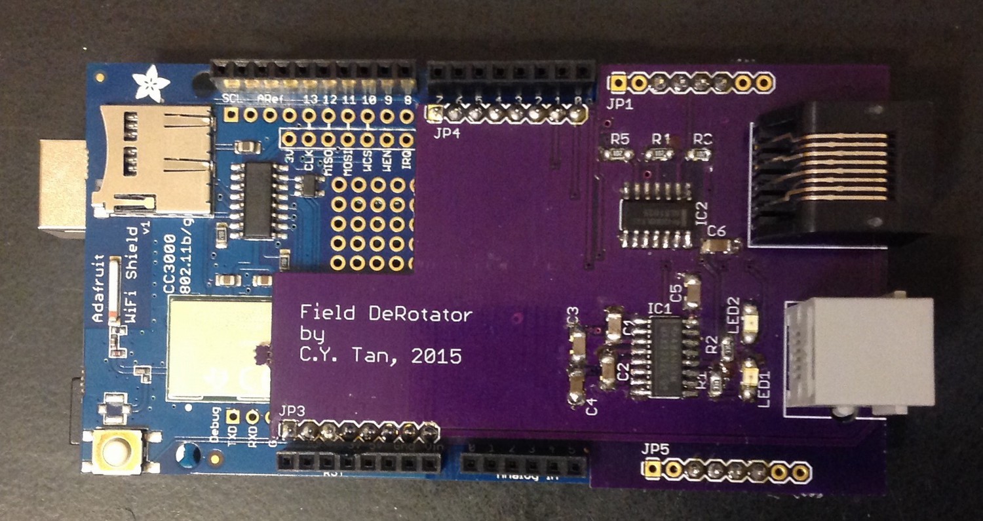
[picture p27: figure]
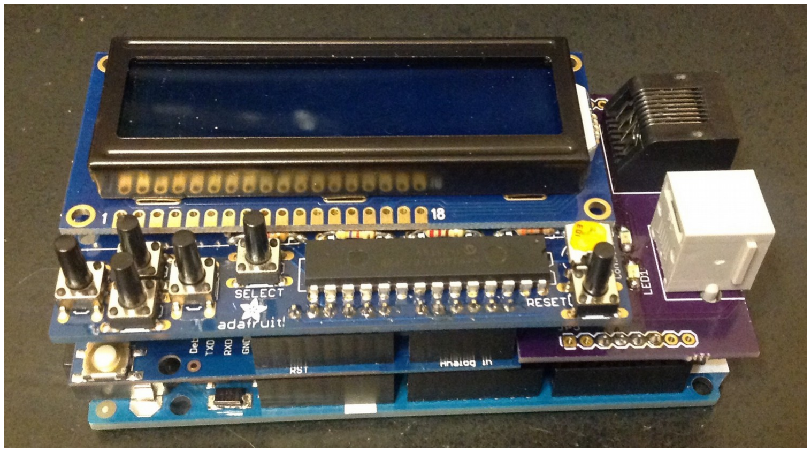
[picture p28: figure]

3 | Field De-rotator Assembly | August 22, 2015

## Controller board

The controller board is soldered onto the WIFIshield and insterted into the MEGA2560 board.

Then the LCD shield is inserted above the WIFIshield

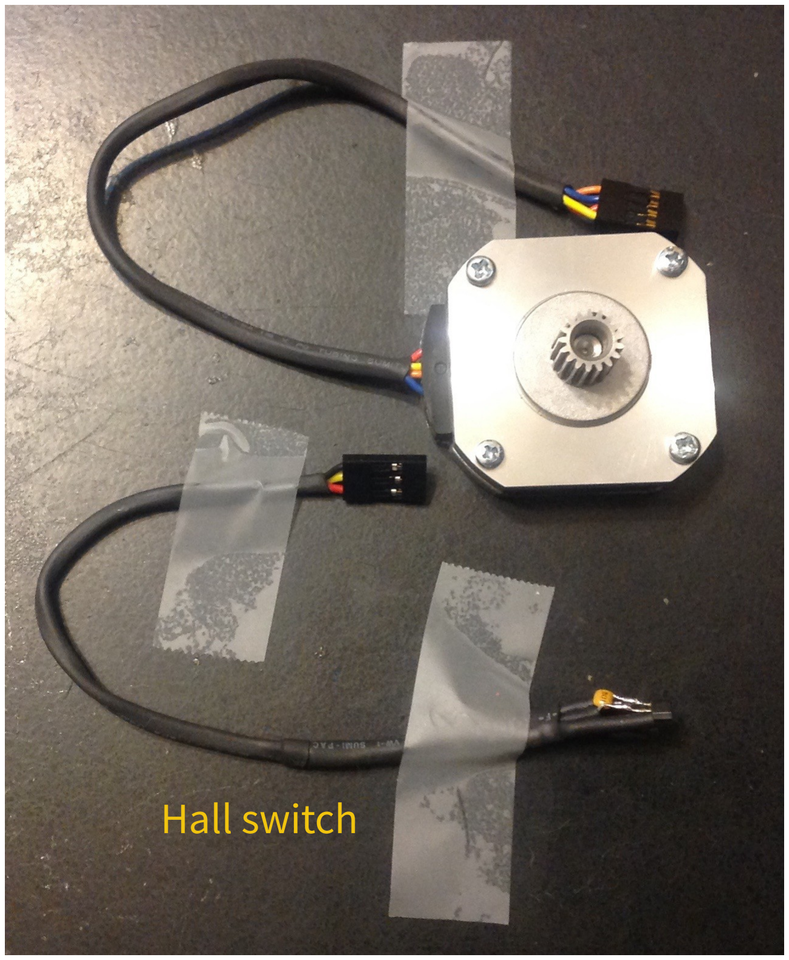
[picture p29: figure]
Hall switch

4 | Field De-rotator Assembly | August 22, 2015

## Hall switch

The Hall switch is soldered to wires and socketed.

A decoupling capacitor 0.1 uF is soldered directly to pins 1 and 2 of the Hall switch.

## Hall switch taped to the cover

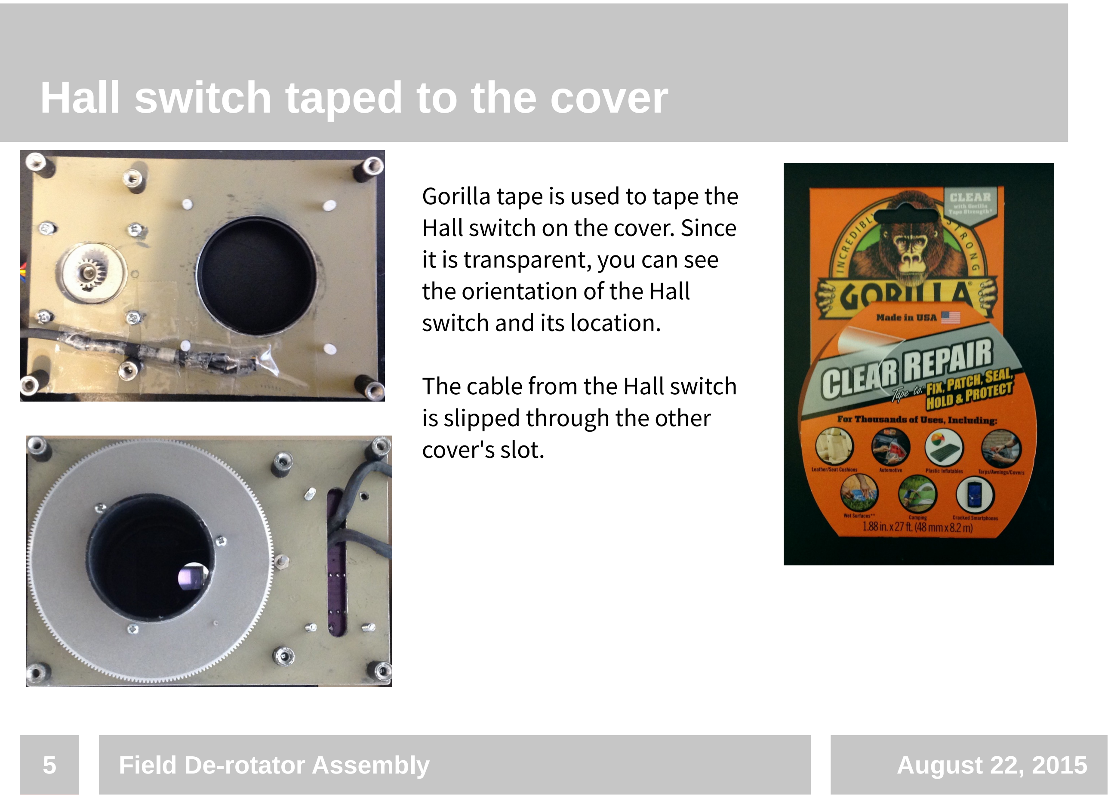
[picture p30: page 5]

5 | Field De-rotator Assembly | August 22, 2015

Gorilla tape is used to tape the Hall switch on the cover. Since it is transparent, you can see the orientation of the Hall switch and its location.

The cable from the Hall switch is slipped through the other cover's slot.

## Taping the Hall switch to the shell

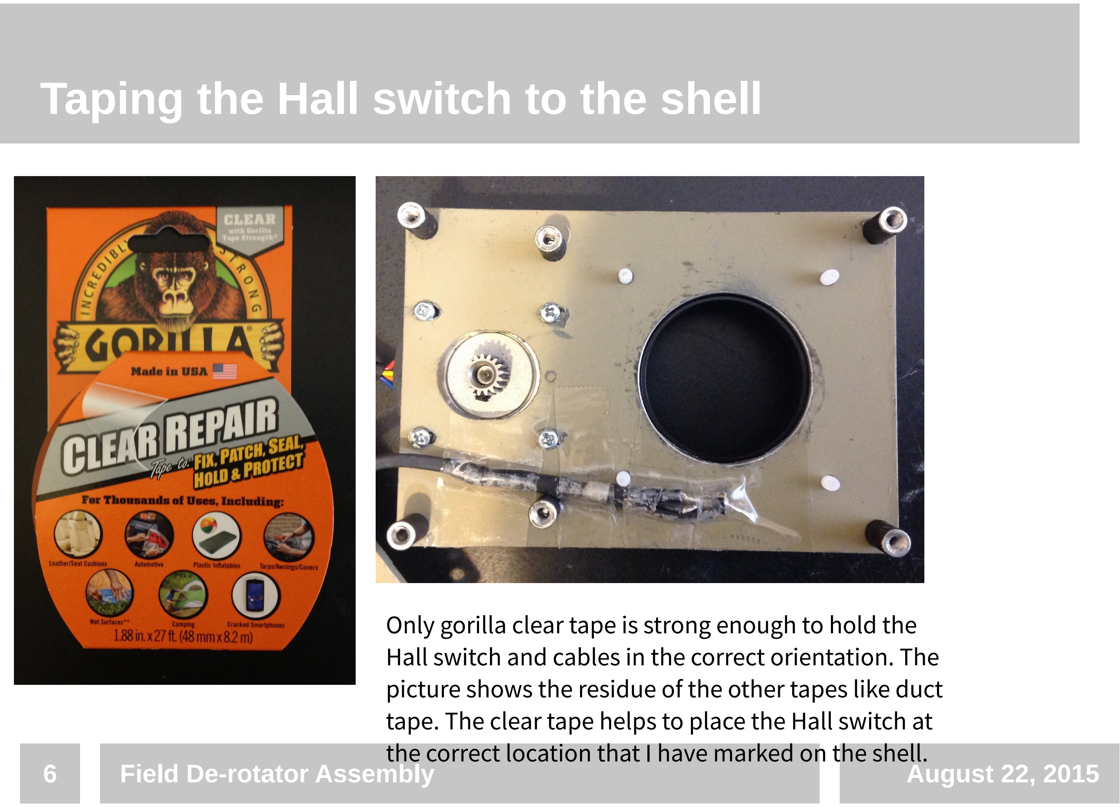
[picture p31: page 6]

6 | Field De-rotator Assembly | August 22, 2015

Only gorilla clear tape is strong enough to hold the Hall switch and cables in the correct orientation. The picture shows the residue of the other tapes like duct tape. The clear tape helps to place the Hall switch at the correct location that I have marked on the shell.

## Assembling the slice case

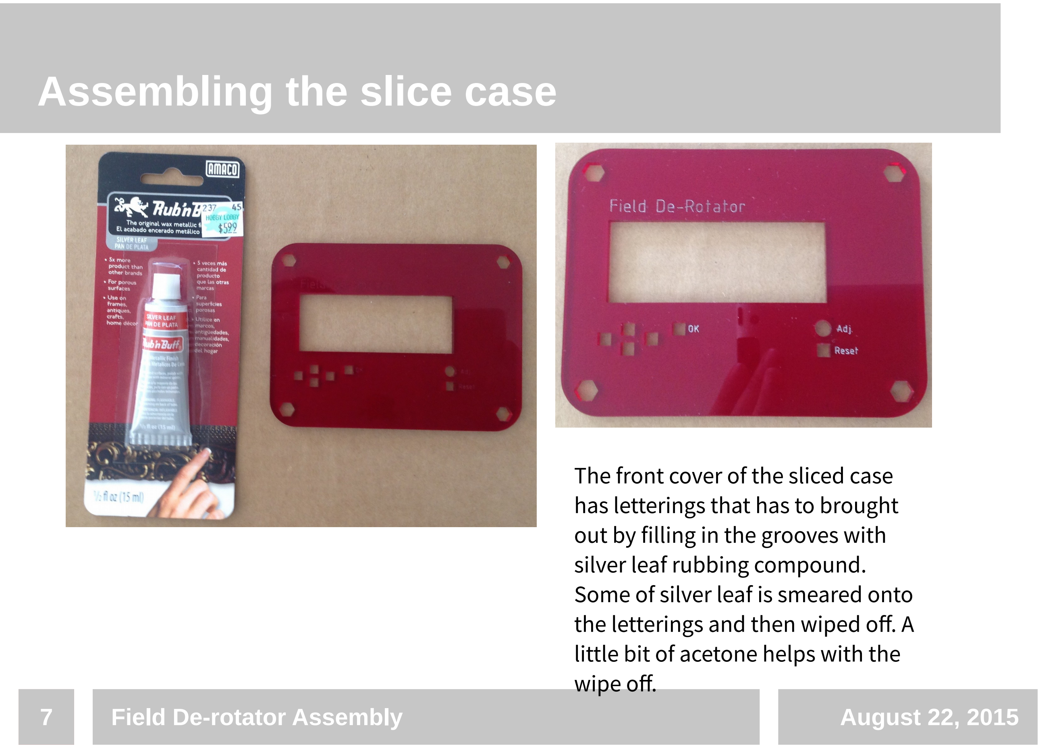
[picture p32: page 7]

7 | Field De-rotator Assembly | August 22, 2015

The front cover of the sliced case has letterings that has to brought out by filling in the grooves with silver leaf rubbing compound. Some of silver leaf is smeared onto the letterings and then wiped off. A little bit of acetone helps with the wipe off.

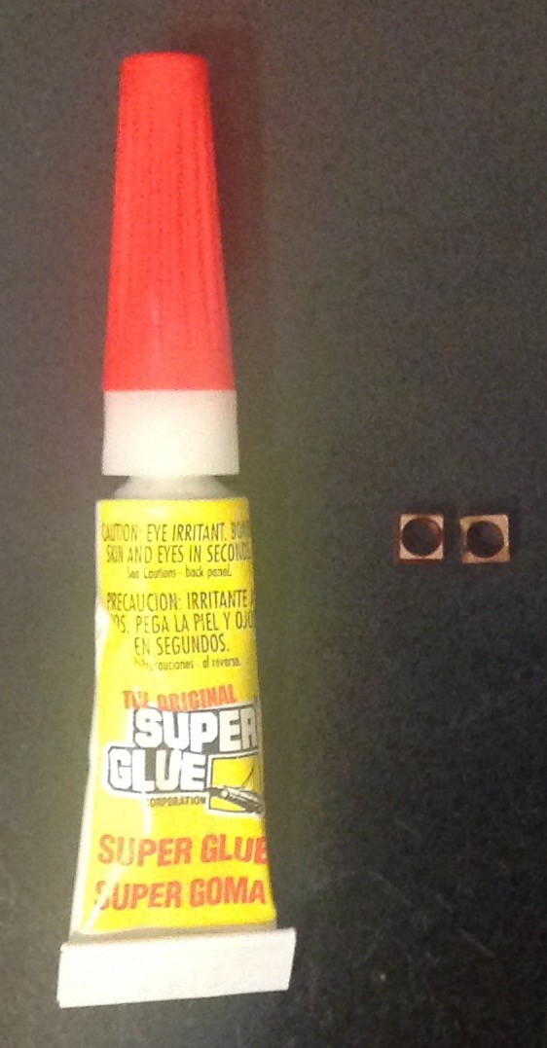
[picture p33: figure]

8 | Field De-rotator Assembly | August 22, 2015

## Making the push button switches

Pushbuttons on the controller are made by supergluing two cubes with holes together. These cubes with holes come from the same plastic that was laser cut with the other case parts.

This assembly is then superglued to the push button stems. Good thing is that the push button stems rotate, so that they can be easily aligned to the square holes on the case cover.

## Building the case

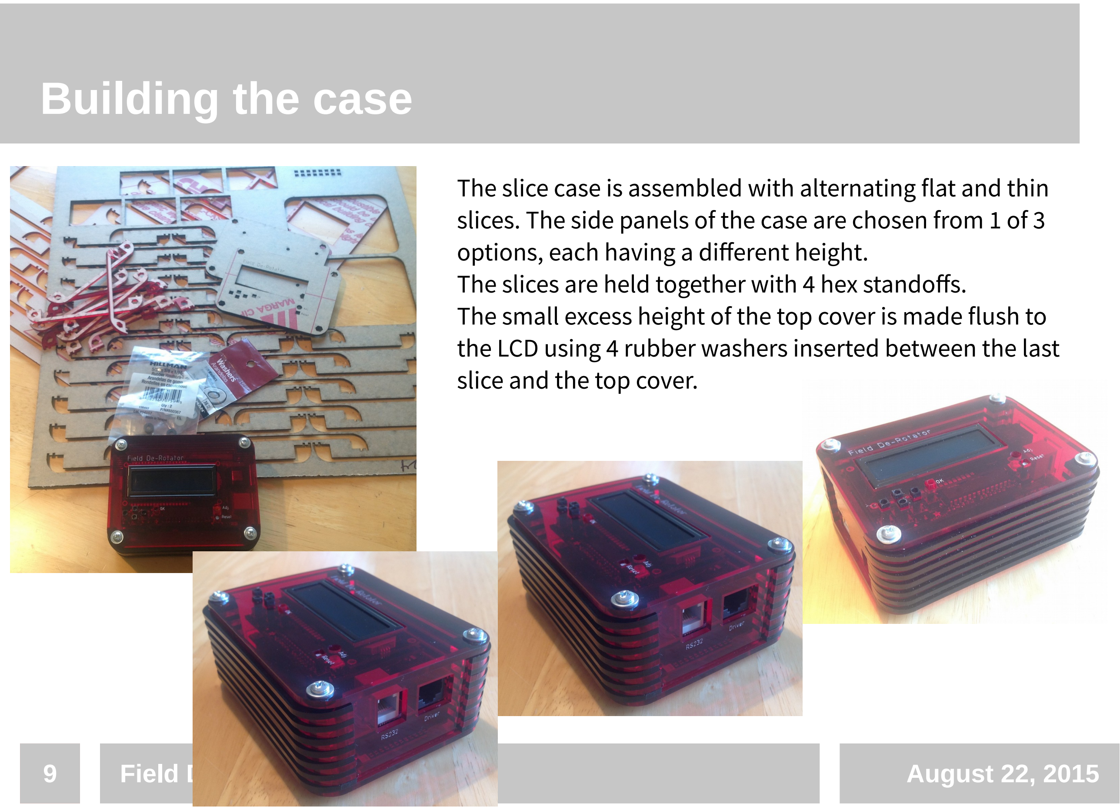
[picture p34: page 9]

9 | Field De-rotator Assembly | August 22, 2015

The slice case is assembled with alternating flat and thin slices. The side panels of the case are chosen from 1 of 3 options, each having a different height.
The slices are held together with 4 hex standoffs.
The small excess height of the top cover is made flush to the LCD using 4 rubber washers inserted between the last slice and the top cover.

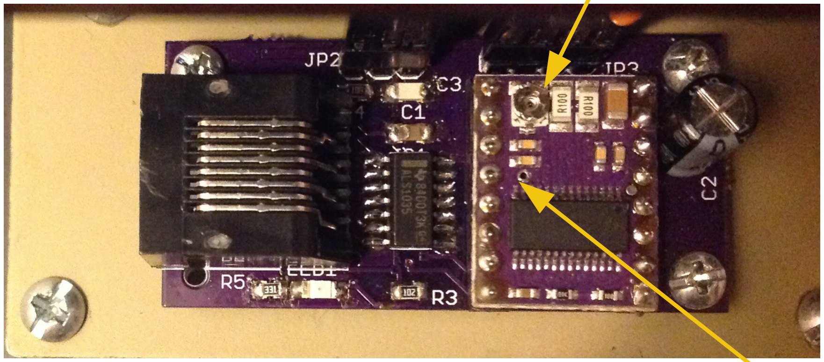
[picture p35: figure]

10 | Field De-rotator Assembly | August 22, 2015

## Making the driver

The voltage on the stepper motor driver must be adjusted with the pot. The Pancake Sanyo motor doesn't like 1A max setting. It gets
hot and whines a lot. So it has been set to 600 mA max. This corresponds to 0.3 V at the test point. See also https://www.pololu.com/product/2133

Adjust here

Measure voltage
here.

11 | Field De-rotator Assembly | August 22, 2015

## Done!

The controller is assembled and it is programmed using a USB cable connect to a computer, and the Arduino JAVA GUI. The controller can now be connected to the derotator. See
- Installing the Field DeRotator
- Field DeRotator Controller User's Guide

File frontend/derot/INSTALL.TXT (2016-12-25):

INSTALL
=====
(Dec 2016)

At this time the code is Mac centric. Although the executable
   derot
can be built without any Mac dependencies by commenting out the Mac
bundle part of the Makefile.

However, logs and help paths will be screwed up.  IMO, to get rid of
Macisms should not be too difficult. But I do not have Linux box or a
Windows box to check this.  The biggest change to make to make derot
not be Mac centric is to get rid of the Mac bundle.

To see where the Mac centric code is, just to a
   grep "__APPLE__" *.cpp *.hpp *.cxx *.h

Build requirements
==============

(1) The boost libraries must be installed.
    On a Mac, use macports
       port install boost

(2) The fltk libraries must be installed. fltk-1.3.4 works. fltk-1.3.3
     is actually quite unstable and and the earliest version that
     works is fltk-1.3.x-r10729.
     Download from www.fltk.org

(3) A dynamic bundler must be installed to make the derot.app bundle
    Download from
    	     https://github.com/auriamg/macdylibbundler

Edits
===
Edit Makefile.FLTK to point to where you've installed fltk. Change this:
     FLTKCONFIG   = ../fltk-1.3.4-1/fltk-config

Edit Makefile to point to where dylibbundler is installed
     DYLIBBUNDLER = ../macdylibbundler-master/dylibbundler

Build
===
	Run
		make

Install
====
The mac bundle
    derot.app
can be moved to /Applications using
    sudo mv derot.app /Applications

Log files
=====
The programme log is found is
    ~/Library/Logs/derot

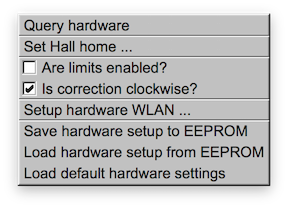
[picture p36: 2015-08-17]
frontend/derot/help/help_interface/pics/hardware_setup.png

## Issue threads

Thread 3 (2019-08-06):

Adafruit CC3000 discontinued problem

cumarit, 2019-08-06:
How can I replace it with the Adafruit WINC1500?
Thank you.
Marcello

cytan299, 2019-08-08:
When I look at the winc1500 when compared to cc3000, it looks like the IRQ and CS pins are not at the same location. You'll have to modify them on the winc1500 board accordingly. The code will have to be updated to so that it uses the winc1500 library and not the cc3000 library.

I don't think it is too difficult for you to do it.

Closed 2019-08-22.

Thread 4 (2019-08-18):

Compiling under Linux

roboticboyer, 2019-08-18:
Good Morning
I compiled the Front-end under Linux Mint 19.1 with some minor changes on the Make file ( I can share the file if requested)

Starting the program, it close immediately with this error message (I can see the GUI only for 1 second)

> segmentation fault

The dump of the error is:
> 0x00005555555d197c in gl_draw(char const*, int) ()

The issue is the below line of code
`DeRotatorGraphics.cpp 432:  gl_draw(buf, -14.0f, -9.5f );`

https://github.com/cytan299/field_derotator/blob/4f215db3dadfd8cf80bc349a19b55723e4416fad/frontend/derot/DeRotatorGraphics.cpp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

I commented the line and the program started to work but I lost the "angle of the derotator"

I'm not expert about FLTK library. Do you know how to fix it?
I think it's something related to the type (float or int) of the x and y coordinates

I'm using the version 1.3.4 of the FLTK library as suggested

Thank you for the support
Gio

cytan299, 2019-08-18:
I just checked the code in MacOSX and I don't see it being broken. I'd suggest uncommenting line 43 and recompiling. I assume that the Makefile has -g option enabled and so you should be able to debug it with lldb.

In lldb, break at line 432 and print out buf. It should look something like this:

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

If you continue and it crashes. You might want to do a
    thread backtrace

to see where in gl_draw() is actually failing.

cytan299, 2019-08-18:
Hi Gio,
  I've run derot through lldb and I did not see it crash. I would suggest that you recompile with the line uncommented. I believe the Makefile has -g enabled so that you can use lldb to see what's going on. Break at line 432 and print out buf. You should see something like this:

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

If it crashes again, try seeing exactly where by doing
   thread backtrace

to see where you are that actually caused the crash.

You may have to enable debugging in FLTK as well so that it will be clear where the problem is.

P.S. there is this odd ball warning that CGContextSaveGState invalid context 0x0 which may be the actual problem. But this doesn't crash on my Mac.

roboticboyer, 2019-08-21:
Hi CY
I made further tests
I think there is a bug inside the `gl_draw` method under linux
I used this work around to fix it
I changed:
```
glDisable(GL_DEPTH_TEST);
 gl_color(FL_GRAY);
 char buf[32];
sprintf(buf, "\u03B6 = % 7.2f deg    ", _z_angle);
gl_draw(buf, -14.0f, -9.5f ); //GB
glEnable(GL_DEPTH_TEST);
```

with
```
fl_color(FL_GRAY);
fl_font(FL_HELVETICA,16);
char buf[32];
sprintf(buf, "\u03B6 = % 7.2f deg    ", _z_angle);
fl_draw(buf, -14, 9);

```
My last concern is where is show the string "buf". I can't see it

thank you
Gio

cytan299, 2019-08-22:
Technically, both  fl_draw(const char*, int x, int y) and fl_draw(const char*, float x, float y) are wrappers to:

 fl_draw(const char*, const int /* length of string*/, int x, int y)

and so I'm surprised that it doesn't crash.

You might want to move the x,y position of the label to see if you see the label somewhere on the GUI.

Sorry, I don't do Linux so I can't really see what you're seeing. But I'll continue looking because I don't believe fl_draw() is the source of the crash.

cytan299, 2019-08-22:
P.S. You seem to have forgotten the minus sign in fl_draw(), i.e. fl_draw(buf, -14, 9) should be fl_draw(buf, -14, -9)

roboticboyer, 2019-08-22:
**1st test**
I tried with `fl_draw(buf, -14, -9)` and others X and Y coordinates but without success

please note that now I'm using `fl_draw` (FLTK) not yet `gl_draw` (openGL)
Could be mixed FL functions/methods with OpenGL ones?

**2nd test**
Again segmentation fault using:
```
const float xg=-14.0f;
const float yg=-9.5f;
glRasterPos2f(xg,yg);
gl_draw(buf, strlen(buf));
```
Probably something related to openGL libraries

roboticboyer, 2019-08-25:
I tested `sprintf(buf, "Dz = % 7.2f deg    ", _z_angle);` but it doesn't fix the issue

I expanded the program window up to 800x800 and used:
 `fl_draw(buf, 20, 500);` but I can't see the text
 `fl_draw(buf, -20, -500);` but I can't see the text

Using `cout << "Debug buf: " << buf <<  "\n";` I see the text on the console, so the variable `buf` is OK

cytan299, 2019-08-25:
I think the problem with using fl_draw() is that it will not draw to the OpenGL context. So you will need to use gl_draw() to see anything. You may be right that there is a bug in the OpenGL implementation in Linux, or Linux requires some more OpenGL initialization that is not needed in Mac OS X. At this point, I’m not sure I have anything else to add or to help you fix this Linux problem because I don’t do Linux.

Closed 2019-10-01.

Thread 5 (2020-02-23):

MIT License

scottwis, 2020-02-23:
Would you consider releasing this under a more permissive license than GPL 3? For example MIT or X11?

I use the The Sky-X Professional to control my imaging setup. That’s mostly because I have a Mac laptop and it’s one of the few things that works on the Mac.

In any case, it has the ability to control  mounts and field rotators, but not support for auto de-rotation as the mount moves.

However, it does  offer a JavaScript scripting interface that has access to both the mount and the rotator.

So, my plan is to take your source, extract the parts for communicating rotational deltas, convert it to JavaScript, and then run it inside TheSkyX pro.

I can make the JS open source, but the plugins in TSX for communicating with the mount and the rotator are not open source.

Thus, if I did that it could be construed as “making a derivative work” and then “linking it with non free software”.

That would be incompatible with the GPL.

However If you were willing to do MIT or something similar, this would not be an issue.

cytan299, 2020-02-24:
Hi Scott,
   I don't understand why a JS code that sits between the rotator and TheSkyX would violate GPL3.

  I would like to leave the license as GPL3 but I'm willing to consider adding an MIT license. However, I'm not familiar with relicensing. Do you have a link to how to do this properly?

cytan

scottwis, 2020-02-24:
If all the contributors came from you, then you can just change the license file to the MIT version and you are good.

After some experiments with TSX, however, I don’t think I actually need you to re-license this.

TSX runs all it’s Java Script on its UI thread and it doesn’t expose anything related to the event loop (no setTimeout or process.nextTick()), so it’s not really amenable to long lived processes. If I write the whole thing in JavaScript it will make the rest of TSX unusable.

What it does support well, however, is communicating over TCP and executing small  scripts to exchange data.

For that case, I can just hack up your code and release my hacks as GPL and I am good (because the non free TSX code is just communicating with the GPL code over a socket), and that’s ok.

So, feel free to close this. Sorry to bug you.

Sent from my iPhone

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

cytan299, 2020-02-24:
Hi Scott,
   Not a problem at all. Actually it is quite flattering to know that you're interested in my code :)

cytan

Closed 2020-02-24.

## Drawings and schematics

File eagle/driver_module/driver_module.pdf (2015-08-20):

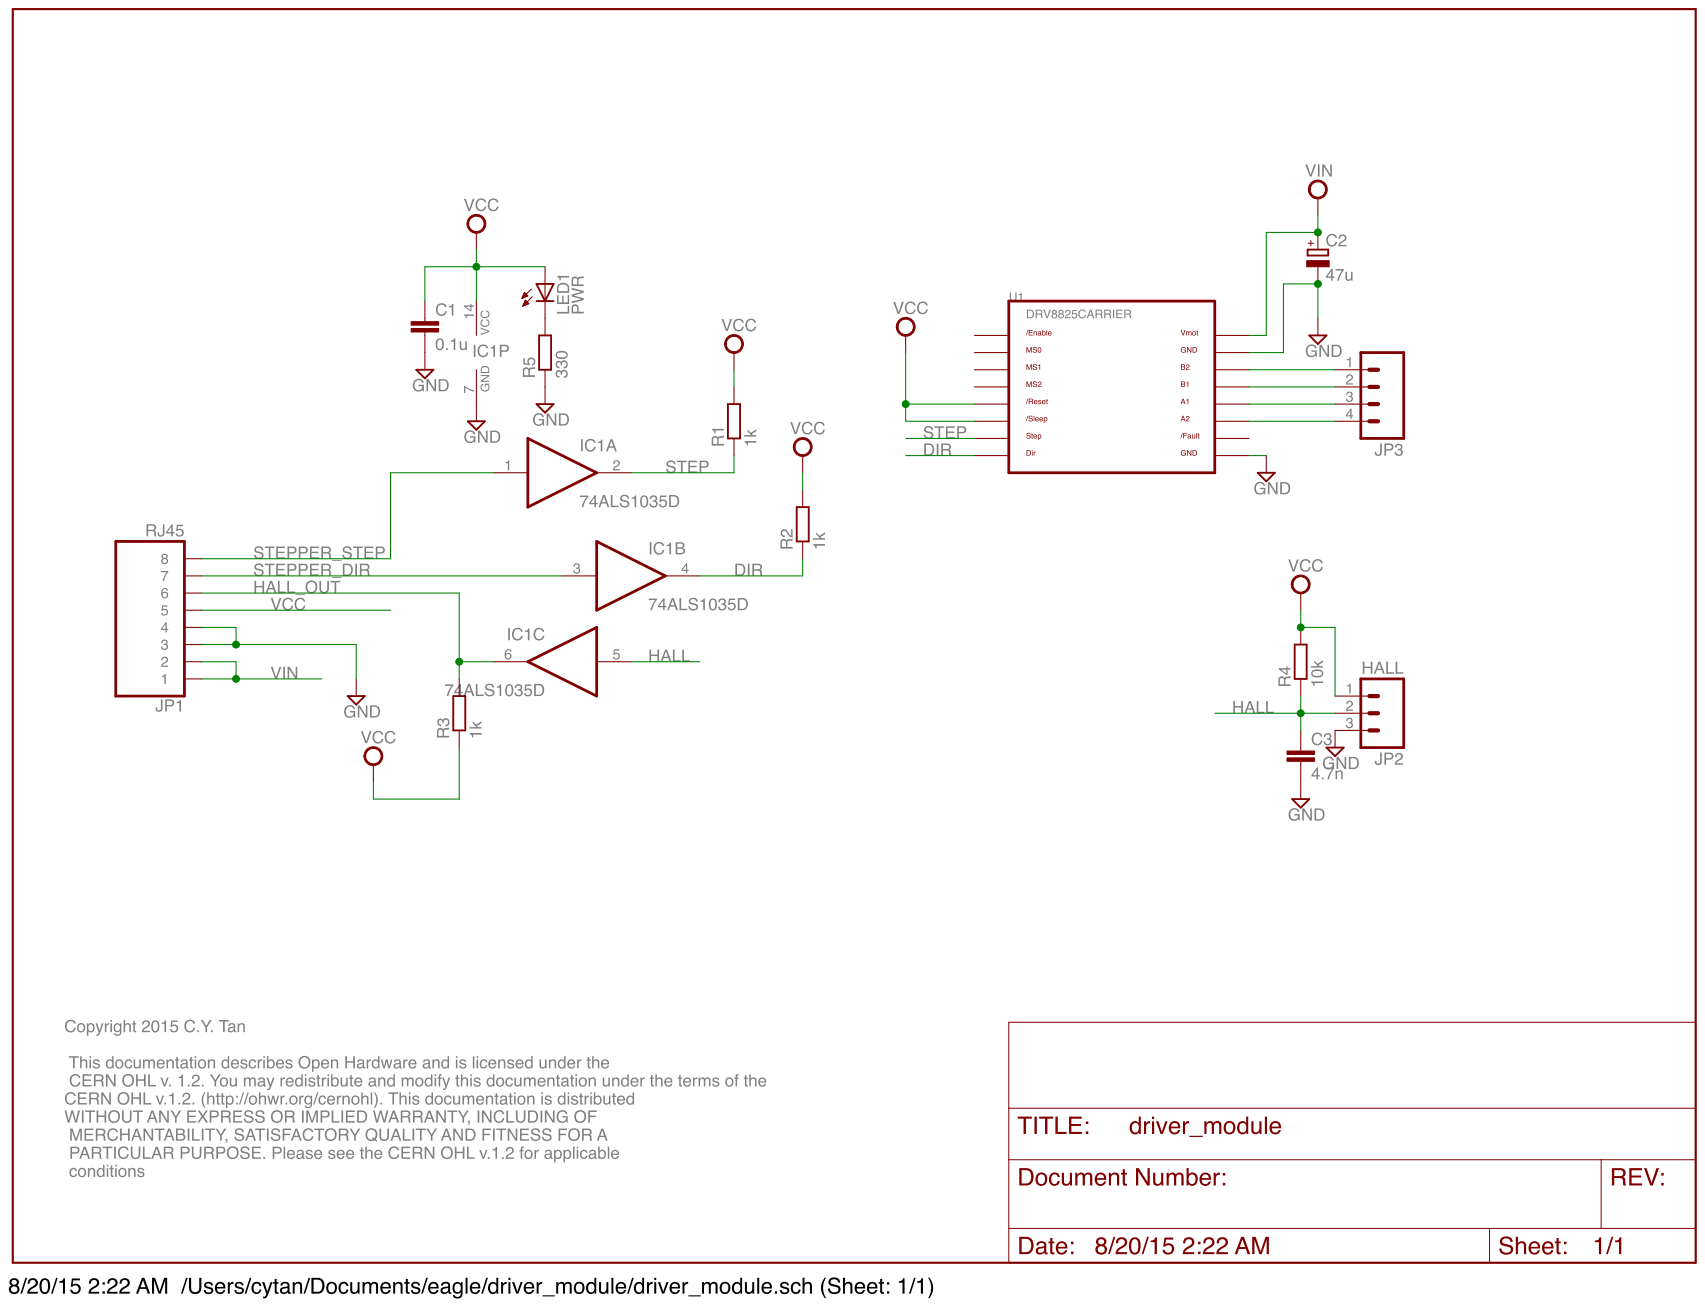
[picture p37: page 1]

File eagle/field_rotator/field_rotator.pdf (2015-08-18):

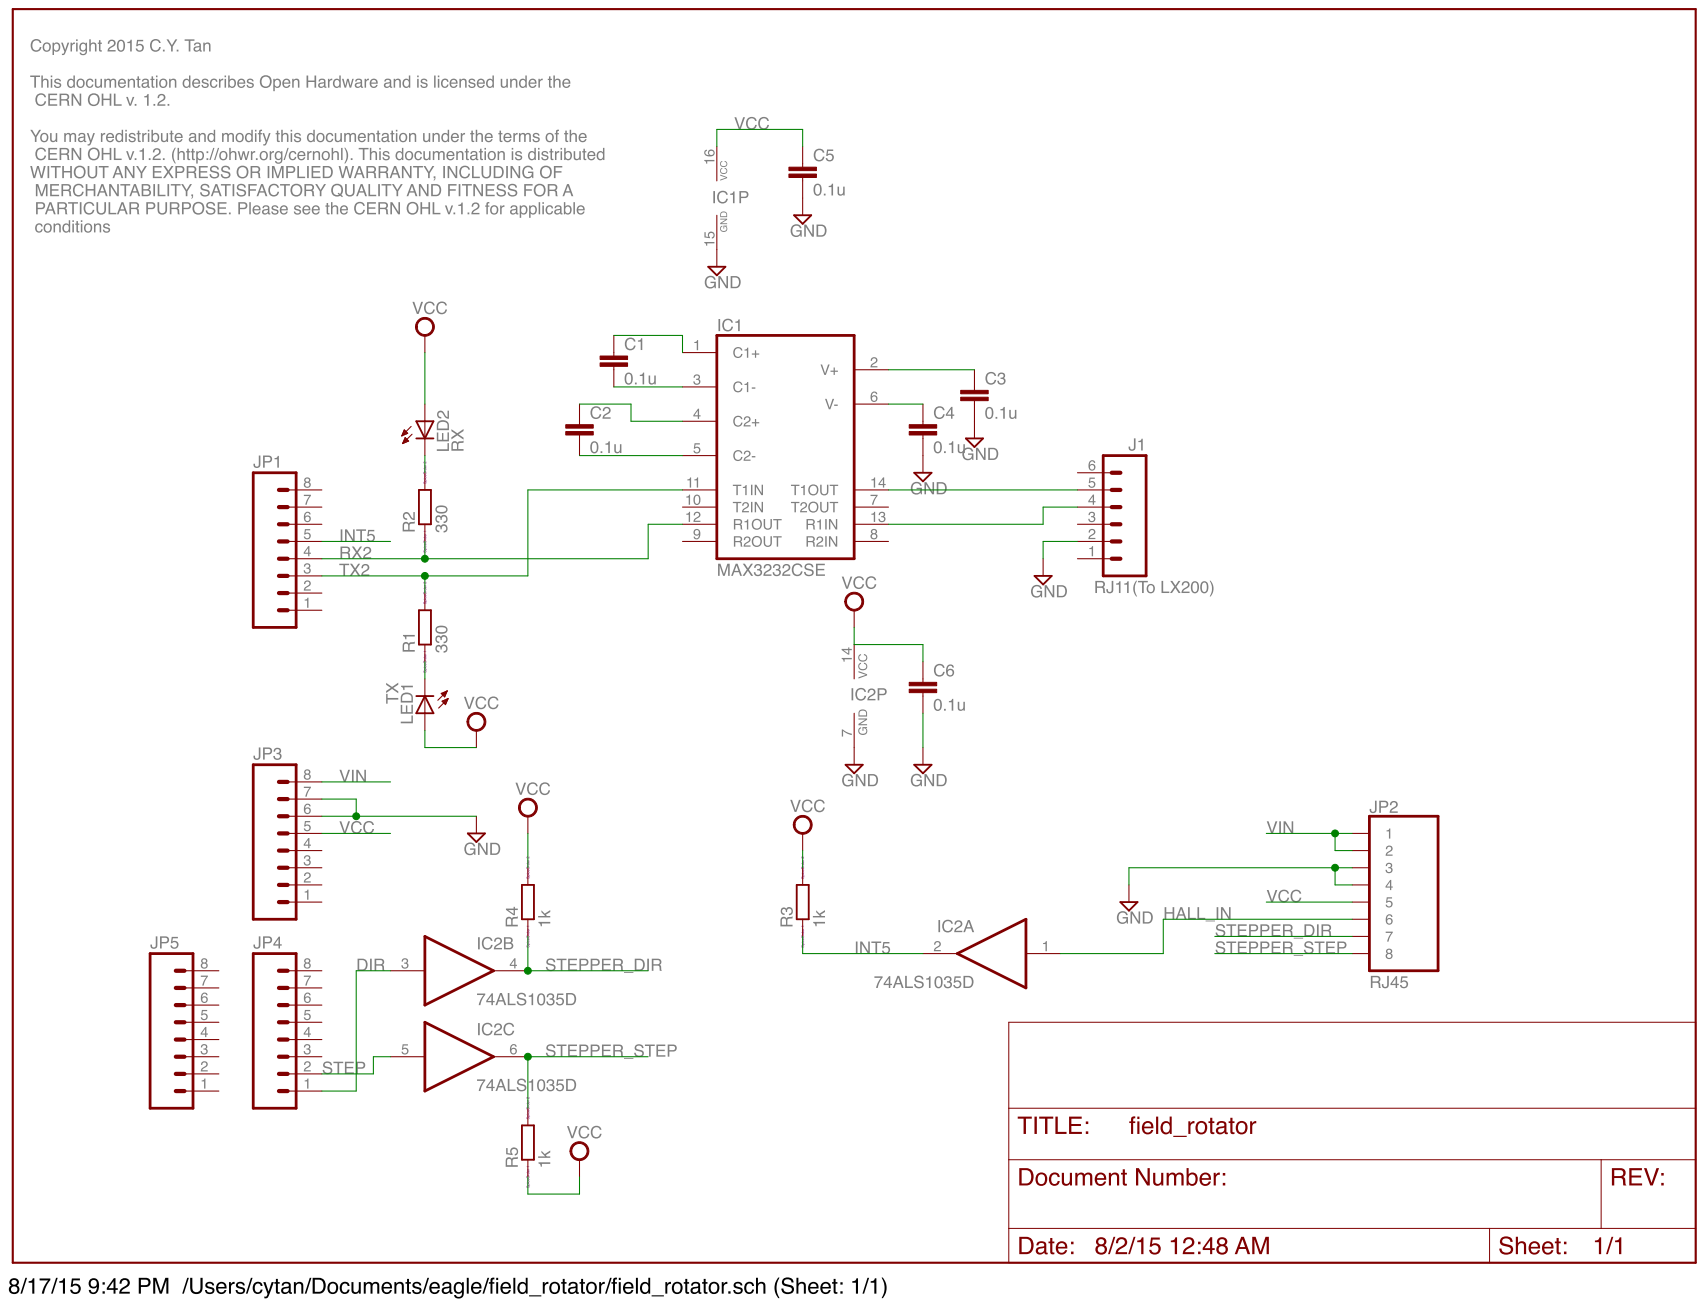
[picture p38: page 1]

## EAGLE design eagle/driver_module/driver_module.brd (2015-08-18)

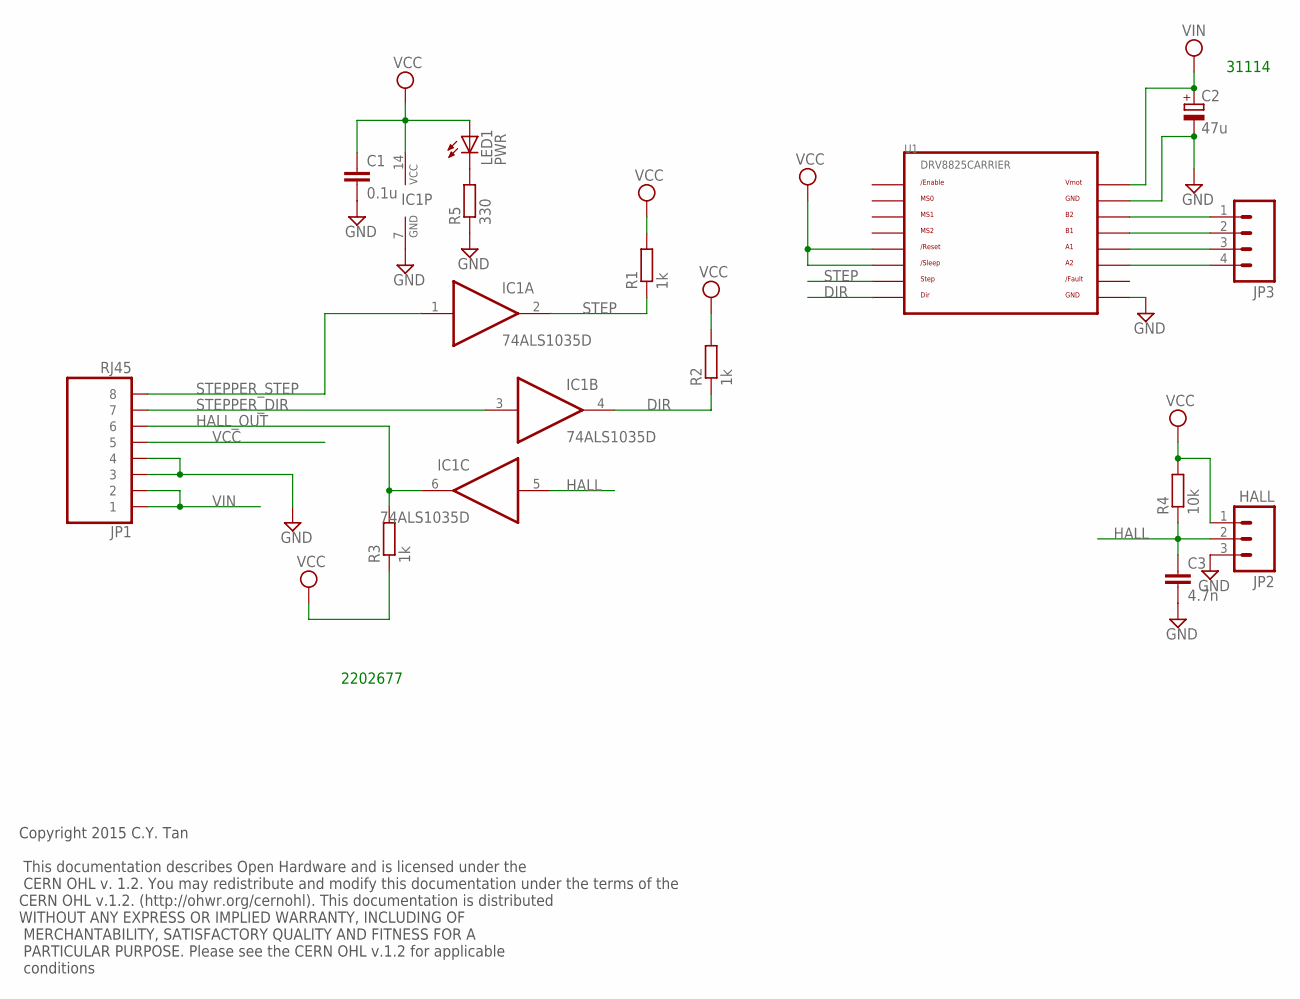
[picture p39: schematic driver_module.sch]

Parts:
C1: 0.1u; C1206
C2: 47u; E2,5-6
C3: 4.7n; C1206
IC1: 74ALS1035D; SO14
JP1: RJ45; RJ45-8
JP2: HALL; 1X03
JP3: M04PTH; 1X04
LED1: PWR; CHIPLED_1206
R1, R2, R3: 1k; M0805
R4: 10k; M0805
R5: 330; M0805
U1: DRV8825CARRIER

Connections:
/FAULT: U1./FAULT
DIR: IC1.4 (O), R2.1, U1.DIR
GND: C1.2, C2.-, C3.2, IC1.7 (GND), JP1.3, JP1.4, JP2.3, R5.1, U1.GND@0 (GND), U1.GND@1 (GND)
HALL: C3.1, IC1.5 (I), JP2.2, R4.1
HALL_OUT: IC1.6 (O), JP1.6, R3.2
unnamed: JP3.1, U1.B2
unnamed: JP3.2, U1.B1
unnamed: LED1.C, R5.2
unnamed: JP3.3, U1.A1
unnamed: JP3.4, U1.A2
STEP: IC1.2 (O), R1.1, U1.STEP
STEPPER_DIR: IC1.3 (I), JP1.7
STEPPER_STEP: IC1.1 (I), JP1.8
VCC: C1.1, IC1.14 (VCC), JP1.5, JP2.1, LED1.A, R1.2, R2.2, R3.1, R4.2, U1./RESET, U1./SLEEP
VIN: C2.+, JP1.1, JP1.2, U1.VMOT

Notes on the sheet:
2202677
31114
Copyright 2015 C.Y. Tan This documentation describes Open Hardware and is licensed under the CERN OHL v. 1.2. You may redistribute and modify this documentation under the terms of the CERN OHL v.1.2. (http://ohwr.org/cernohl). This documentation is distributed WITHOUT ANY EXPRESS OR IMPLIED WARRANT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

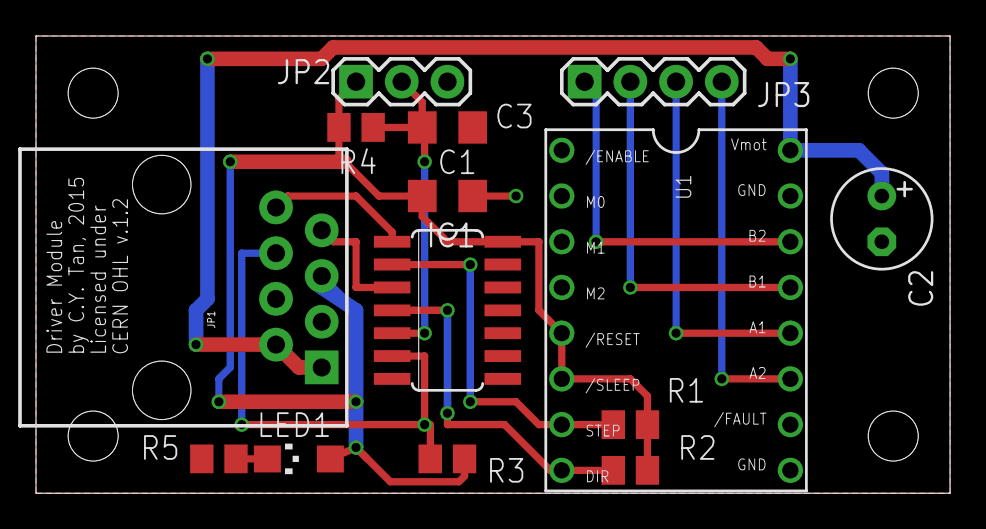
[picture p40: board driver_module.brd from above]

Board: 2 copper layers, 50.8 x 25.4 mm, 14 parts (0 on the bottom side), 14 nets.

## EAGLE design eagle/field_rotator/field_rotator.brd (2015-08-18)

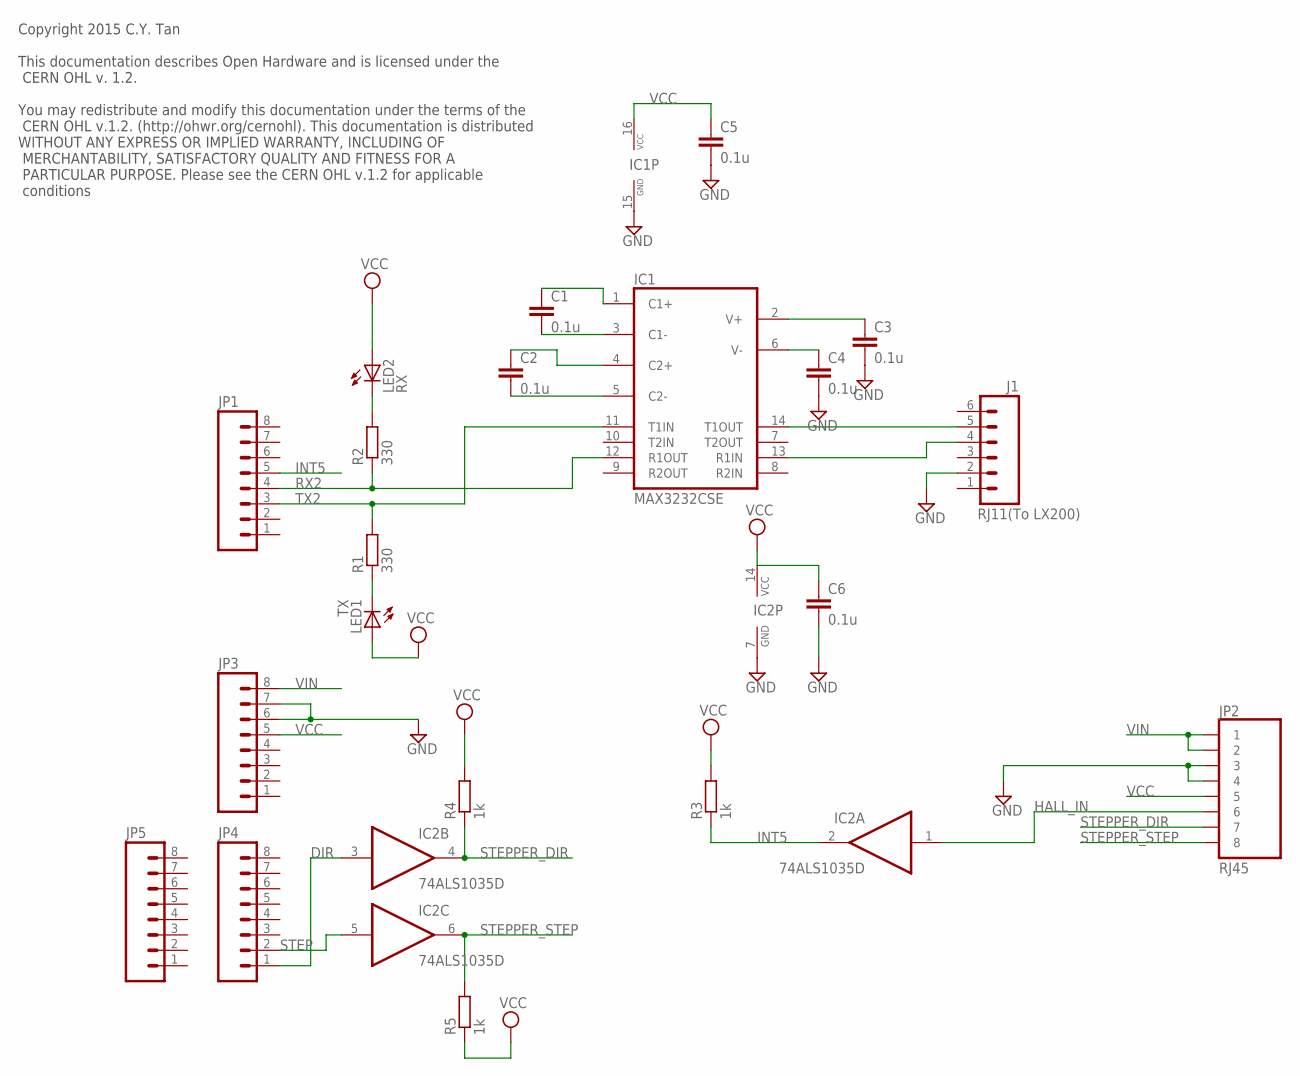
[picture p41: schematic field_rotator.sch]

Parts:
C1, C2, C3, C4, C5, C6: 0.1u; C1206
IC1: MAX3232CSE; SO16
IC2: 74ALS1035D; SO14
J1: RJ11(To LX200); RJ11-6
JP1, JP3, JP4, JP5: M08SILK_FEMALE_PTH; 1X08
JP2: RJ45; RJ45-8
LED1: TX; CHIPLED_1206
LED2: RX; CHIPLED_1206
R1, R2: 330; R0805
R3, R4, R5: 1k; R0805

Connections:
DIR: IC2.3 (I), JP4.1
GND: C3.2, C4.2, C5.2, C6.2, IC1.15 (GND), IC2.7 (GND), J1.2, JP2.3, JP2.4, JP3.6, JP3.7
HALL_IN: IC2.1 (I), JP2.6
INT5: IC2.2 (O), JP1.5, R3.1
unnamed: C1.1, IC1.1 (C1+)
unnamed: C1.2, IC1.3 (C1-)
unnamed: C2.1, IC1.4 (C2+)
unnamed: C2.2, IC1.5 (C2-)
unnamed: C3.1, IC1.2 (V+)
unnamed: C4.1, IC1.6 (V-)
unnamed: LED1.C, R1.1
unnamed: LED2.C, R2.2
unnamed: IC1.14 (T1OUT), J1.5
unnamed: IC1.13 (R1IN), J1.4
RX2: IC1.12 (R1OUT), JP1.4, R2.1
STEP: IC2.5 (I), JP4.2
STEPPER_DIR: IC2.4 (O), JP2.7, R4.1
STEPPER_STEP: IC2.6 (O), JP2.8, R5.2
TX2: IC1.11 (T1IN), JP1.3, R1.2
VCC: C5.1, C6.1, IC1.16 (VCC), IC2.14 (VCC), JP2.5, JP3.5, LED1.A, LED2.A, R3.2, R4.2, R5.1
VIN: JP2.1, JP2.2, JP3.8

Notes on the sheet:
Copyright 2015 C.Y. Tan This documentation describes Open Hardware and is licensed under the CERN OHL v. 1.2. You may redistribute and modify this documentation under the terms of the CERN OHL v.1.2. (http://ohwr.org/cernohl). This documentation is distributed WITHOUT ANY EXPRESS OR IMPLIED WARRANT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

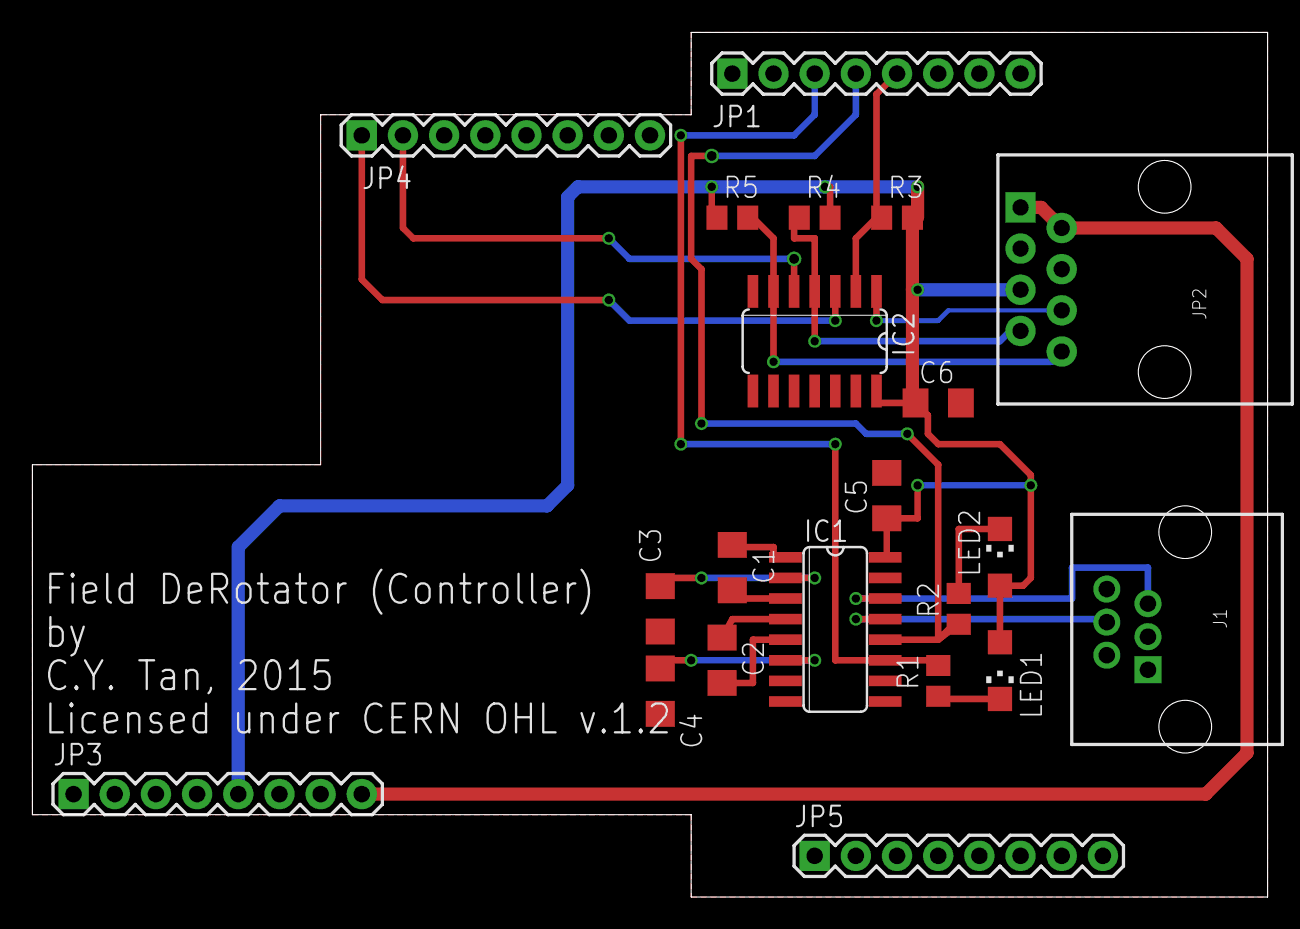
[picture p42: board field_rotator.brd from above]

Board: 2 copper layers, 76.2 x 53.3 mm, 21 parts (0 on the bottom side), 21 nets.

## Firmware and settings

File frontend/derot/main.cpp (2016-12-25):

/*$Id$*/
/*
    derot is the GUI frontend that controls the field derotator
    Copyright (C) 2015  C.Y. Tan
    Contact: cytan299@yahoo.com

    This file is part of derot

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
*/

/* operating system header files (use <> for make depend) */
#include <iostream>

/* general system header files (use "" for make depend) */
#include <config.h>
#include <FL/Fl.H>

#include "boost/filesystem.hpp"
#include "boost/program_options.hpp"

/* local include files (use "") */
#include "constants.h"

#include "TCPClient.hpp"
#include "SerialClient.hpp"
#include "logging.hpp"

#include "DeRotatorUI.h"
#include "MessageSink.hpp"
#include "DeRotatorCMD.hpp"


using namespace std;

/**********************************************************************
NAME

	log_init - initialize logging to write into both log file and
		   stderr
		

		   
SYNOPSIS

	log_init() sets up the boost logger so that messages are
	written into both a log file and stderr.

	The log files are named
		derot_%DATE%_%TIME%.log

	where %DATE% is in the form year-month-day
	      %TIME% is in the form hour:minute:seconds

ARGUMENTS
	log_init(
	  display	- pointer to the Messages text display window
	  message	- pointer to the text buffer of the Messages window
	  message_dir	- directory to write the messages	
	)

AUTHOR
	C.Y. Tan

SEE ALSO

**********************************************************************/

void log_init(Fl_Text_Display* const display,
	      Fl_Text_Buffer* const message,
	      const char* message_dir)
{

  using namespace boost;
  using namespace boost::filesystem;

  // check that the directory exists
  path p(message_dir);
  if(!exists(p)){
    // doesn't exist, so create it
    create_directory(p);
  }
  
  string filename;
  posix_time::ptime t = posix_time::second_clock::local_time(); 
  filename =
    string(message_dir)
    + "/"
    + "derot_"
    + to_simple_string(t.date()) + "_"
    + to_simple_string(t.time_of_day())
    + ".log";

  typedef sinks::synchronous_sink< sinks::text_ostream_backend > text_sink;
  boost::shared_ptr< text_sink > sink = boost::make_shared< text_sink >();
  
  sink->locked_backend()->
    add_stream(
	       boost::make_shared< std::ofstream >(filename));
  
  sink->set_formatter(
		      expr::stream
		      << expr::format_date_time< boost::posix_time::ptime >("TimeStamp", "%Y-%m-%d %H:%M:%S")
		      << ": <" << logging::trivial::severity
		      << "> " << expr::smessage
		      );
  
  sink->locked_backend()->auto_flush(true);
  logging::core::get()->add_sink(sink);
  
  namespace sinks = boost::log::sinks;

  MessageSink::Init(display, message);

  typedef sinks::synchronous_sink<MessageSink> sink_t;
  boost::shared_ptr<sink_t> sink1(new sink_t());
  boost::shared_ptr<boost::log::core> logc=boost::log::core::get();
  logc->add_sink(sink1);

#ifdef AAAAAAAA
  // spit the messages to both log file and stderr
  logging::add_console_log(std::cerr, boost::log::keywords::format = (
     		      expr::stream
		      << expr::format_date_time< boost::posix_time::ptime >("TimeStamp", "%Y-%m-%d %H:%M:%S")
		      << ": <" << logging::trivial::severity
		      << "> " << expr::smessage
								      ));
#endif
}

/**********************************************************************
NAME

	process_options - process the command line options

		

		   
SYNOPSIS

	process_options() processes the command line options. The
	options are:

	  -h [ --help ]          this message
	  -s [ --srange ] arg    start and stop in steps (separated by a space)
	  -d [ --drange ] arg    start and stop in degrees (separated by a space)
	  -t [ --time ] arg      time to complete from start to stop
	  -H [ --Home ]          go home
	  -v [ --version ]       print version


ARGUMENTS
	process_options(
		argc		- the number of arguments	
		argv		- the array containing the options
	)			- returns 1 if the commandline options
				  are to be processed.

AUTHOR
	C.Y. Tan

SEE ALSO

**********************************************************************/


int process_options(int argc, char **argv)
{
  bool is_got_range = false;
  bool is_got_time = false;
    
  // for the options
  string ip; // ip address
  string serial; // serial line
  
  int64_t sr[] = {0, 0};
  vector<int64_t> srange(&sr[0], &sr[0]+2); // start, stop in steps

  double dr[] = {0.0, 0.0};
  vector<double> drange(&dr[0], &dr[0]+2); //start, stop in degrees

  int64_t steps = 0;
  double degrees = 0;

  double time; // in seconds

  double omega; // rad/s (Earth's rotation rate)

  using boost::lexical_cast;    
  namespace po = boost::program_options;
  // derot command line options
  po::options_description generic("options");
  generic.add_options()
    ("help,h", "this message")
    ("ip,i", po::value<string>(&ip), "ip address of derotator")
    ("Serial,S", po::value<string>(&serial), "serial device to derotator")
    ("srange,s", po::value<vector<int64_t> >(&srange)->multitoken(),
     "start and stop in steps (separated by a space)")
    ("drange,d", po::value<vector<double> >(&drange)->multitoken(),
     "start and stop in degrees (separated by a space)")
    ("gotoD,D", po::value<double>(&degrees), "goto degrees w.r.t. home")
    ("gotoS,G", po::value<int64_t>(&steps), "goto steps w.r.t. home")        
    ("time,t", po::value<double>(&time),
     "time to complete from start to stop in seconds")
    ("omega,o", po::value<double>(&omega)->default_value(OMEGA),
     "rotation rate of the earth in rad/s")
    ("version,v", "print version")
    ;

  po::options_description cmdline_options;
  cmdline_options.add(generic);

  po::variables_map vm;    
  po::notify(vm);
  po::store(po::command_line_parser(argc, argv).options(cmdline_options).run(), vm);

  po::notify(vm);

  if(vm.count("help")){
    cerr << "derot version " << PROJECT_VERSION << "\n";
    cerr << "*** To start up the GUI, do not apply any switches ***\n";
    cerr << cmdline_options << "\n";
    return 1;
  }

  if(vm.count("version")){
    cerr << "derot version " << PROJECT_VERSION << "\n";
    return 1;
  }  

  if((ip.size() == 0) && (serial.size() == 0)){
    throw string("process_options(): IP or serial device must be provided");
  }

  DeRotatorCMD dcmd;

  if(vm.count("ip")){
    if(dcmd.Connect2Wifi(ip.c_str()) != 0){
      throw string("process_options(): Connect2Wifi(): failed\n");
    }
  }

  if(vm.count("Serial")){
    if(dcmd.Connect2Serial(serial.c_str()) != 0){
      throw string("process_options(): Connect2Serial(): failed\n");      
    }
  }
  
  if(vm.count("srange")){
    // convert to degrees
    drange[0] = srange[0]*MECHANICAL_STEPSIZE;
    drange[1] = srange[1]*MECHANICAL_STEPSIZE;
    is_got_range = true;
  }


  if(vm.count("drange")){
    is_got_range = true;    
  }

  if(vm.count("gotoD")){
    if(dcmd.Goto(degrees) != 0){
      throw string("process_options(): Goto(): failed\n");      
    }
    return 1;
  }

  if(vm.count("gotoS")){
    if(dcmd.Goto(steps*MECHANICAL_STEPSIZE) != 0){
      throw string("process_options(): Goto(): failed\n");      
    }
    return 1;
  }

  if(vm.count("time")){
    is_got_time = true;    
  }


  if(is_got_range || is_got_time){
    if(dcmd.Goto(drange[0], drange[1], time) !=0){
      throw string("process_options(): Goto(): failed\n");      
    }
    return 1;
  }

  if(vm.count("omega")){
    if(dcmd.SetOmega(omega) != 0){
      throw string("process_options(): SetOmega(): failed\n");      
    }
    return 1;
  }

  return 0;
}

/**********************************************************************
NAME

	derot - GUI to connect to the field derotator via either wifi
		or serial port.

		   
SYNOPSIS
	derot is the GUI frontend that the user uses to connect to the
	field derotator either via wifi or serial port.

AUTHOR
	C.Y. Tan

REVISION
	$Revision$

SEE ALSO

**********************************************************************/

int main(int argc, char **argv)
{

  using namespace logging::trivial;
  src::severity_logger< severity_level > lg;

  try{

    if(argc > 1){
      if(process_options(argc, argv) == 1){
	return 0;
      }
    }

    DeRotatorUI* derotatorUI = new DeRotatorUI;
    /*
      I have to give DeRotatorGraphics the pointer to the derotatorUI
      because I have to update the steps and deg boxes in the interface
      when the user moves the camera shell outline. Unfortunately,there
      is other way to do this when using the GUI builder Fluid.
    */
    derotatorUI->derotator_graphics->SetDeRotatorUI(derotatorUI);

    // Now initialize the logging system so that error messages are
    // displayed in the Messages window and to a file

    #ifdef __APPLE__
      log_init(derotatorUI->Messages,
	       derotatorUI->_message_buffer,
	       (string(getenv("HOME"))+"/Library/Logs/derot").c_str());
    #else
      log_init(derotatorUI->Messages,
	       derotatorUI->_message_buffer,
	       "/tmp/derot");
    #endif  
    logging::add_common_attributes();

    Fl::visual(FL_DOUBLE | FL_INDEX);
    /*
      show the UI.
      If command line options need to be processed, use
		derotatorUI->show(argc, argv);
      
    */
    derotatorUI->show();

    // write a start up message in the Message window
    string start_message = string("DeRotator by C.Y. Tan\nVersion: ")+string(PROJECT_VERSION)+string("\n");
    MessageSink::Write(start_message);

    Fl::run();  
  }
  catch(string& s){
    LOG_ERROR <<  "error: " << s << "\n";
    return -1;
  }  
  catch(exception& e){
      LOG_ERROR <<  "error: " << e.what() << "\n";
    return -1;
  }
  catch(...){
    LOG_ERROR << "Unknown exception\n";
    return -1;
  }

  return 0;
}

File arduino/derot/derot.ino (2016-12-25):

/*$Id$*/
/*
    derot is the controller code for the Arduino MEGA2560
    Copyright (C) 2015  C.Y. Tan
    Contact: cytan299@yahoo.com

    This file is part of derot

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
*/

/* operating system header files (use <> for make depend) */
#include <EEPROM.h>
#include <string.h>
#include <math.h>

/* general system header files (use "" for make depend) */

#include "Adafruit_CC3000.h"
#include "ccspi.h"
#include "SPI.h"
#include "Arduino.h"
#include "AccelStepper.h"

#include "Wire.h"
#include "Adafruit_MCP23017.h"
#include "Adafruit_RGBLCDShield.h"
#include "menuADAFRUITLCD.h"
#include "keyADAFRUITStream.h"
#include "chainStream.h"

/* local include files (use "") */
#include "Telescope.h"
#include "BaseServer.h"
#include "TCPServer.h"
#include "SerialServer.h" 
#include "DeRotator.h"
#include "UserIO.h"


/**********************************************************************
  Define the number of teeth on each gear in the de-rotator mechanism
 **********************************************************************/  

#define Td 		17.0   // number of teeth of gear on the stepper
#define T1C		41.0   // number of teeth connected to Td
#define T2C		16.0   // number of teeth on top T1C
#define Tf		200.0  // number of teeth connected to T1C


#define GEAR_RATIO	T1C/Td*Tf/T2C

/*
   number of stepper motor steps to turn 360 deg
*/
#define STEPPER_360	200.0

/*
   the mechanical step size in deg/step

	The default mechanical step size is calculated as follows:
		# of teeth on stepper motor = 17 = Td
		# of teeth on gear that connects to Td, T1C  = 41 
		# of teeth on gear that sits on top of T1C, T2C = 16 
		# of teeth on gear that connects to T2C, Tf  = 200

	The final gear ratio is:
		T1C/Td * Tf/T2C = (41/17)*(200/16) = 30.14705882

	i.e. 1 360 degree turn of the final gear (Tf) requires
	30.14705882 turns of the drive gear (Td).
	=> 1 turn of Td gives 360.0/30.1405882 = 11.94146341 degrees
	of Tf

	The stepper motor takes 200 steps to make 1 turn (because it
	is 1.8 deg/step and thus 360/1.8 = 200), this means 1 step of
	the stepper motor gives: 11.94146341/200.0 = 0.0597 deg/step

	For accuracy: the default mechanical stepsize is
		mechanical_stepsize = 360.0/(T1C/Td*Tf/T2C)/(200.0) =
		0.05970731707 deg/step
*/
#define MECHANICAL_STEPSIZE	360.0/(GEAR_RATIO*STEPPER_360)

UserIO userio;
Telescope telescope;
DeRotator derotator(&telescope, MECHANICAL_STEPSIZE);
TCPServer tcpServer(&userio, &derotator);
SerialServer serialServer(&userio, &derotator);


/**********************************************************************
NAME

	derot - calculates the angular speed required to correct for
		field rotation. The angular speed is applied to the
		stepper motor.
		   
SYNOPSIS
	
	derot calculates the angular speed required to correct
	for field rotation. This angular speed is applied to the
	stepper motor.
	
AUTHOR
	C.Y. Tan

REVISION
	$Revision$

SEE ALSO

**********************************************************************/

void setup()
{

  Serial.begin(115200);
  while(!Serial);
  Serial.println(F("Serial port is open"));
  
  userio.Init(&derotator, &telescope, &tcpServer);
  userio.ShowStartupMessage();
  
  if(telescope.Connect() != 0){
    userio.Print("Cannot connect ", "to telescope", 2000);
    Serial.print(F("setup(): Cannot connect to telescope\n"));
  }
  else {
    Serial.print(F("Connected to telescope\n"));
  }
}

void loop()
{
  userio.ServiceButtons();
  userio.ServiceWifi();
  userio.ServiceDeRotator();
  userio.ServiceSetup();
  userio.ServiceOtherCommands();
  
  serialServer.ServiceLoop();
}

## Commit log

2015-08-17 Create arduino
2015-08-17 removed arduino
2015-08-17 created arduino/derot directory
2015-08-17 Added arduino/derot
2015-08-17 removed arduino/derot
2015-08-17 Added arduino/lib/BaseServer
2015-08-17 Added arduino/lib/DeRotator
2015-08-17 Added arduino/lib/TCPServer
2015-08-17 Added arduino/lib/Telescopes
2015-08-17 Added arduino/lib/UserIO
2015-08-18 Added bom and field derotator formula
    [bom.ods]
2015-08-18 Added eagle files
    [driver_module.brd, driver_module.sch, field_rotator.brd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]
2015-08-18 Added files to arduino_case and emachine_shop
2015-08-18 Added modified library files from Adafruit and Arduino
2015-08-18 Updated arduino/README.md
2015-08-18 Updated arduino/README.md, arduino/lib/README.md
2015-08-18 Updated arduino_case/README.md
2015-08-18 Updated bom/README.md
2015-08-18 Updated arduino/README.md arduino/lib/README.md
2015-08-19 Updated arduino/lib/README.md
2015-08-19 Updated README.md and bom/README.md
2015-08-20 Updated eagle/driver_module schematic
    [driver_module.sch]
2015-08-23 Updated controller.pdf to include making of pushbutton switch button
2015-10-11 arduino/lib: Modified BaseServer, SerialServer, TCPServer, UserIO libraries so that reply_packets have a status that actually indicates the status of the derotator rather than always REPLY_OK.
2015-10-11 frontend: Modified frontend so that the user can now set the displayed camera angle to match the real camera. Internally, error messages about the status of the derotator are now shown in the log sig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
2015-10-24 arduino: Fixed problem that derotator would hang after 1 hour. Fixed a cosmetic bug in the lcd display.
2015-10-24 arduino: Updated ReplyPacket.hpp: Changed the defines REPLY_DEROTATOR_* defines to constants that start from -100.
2015-10-31 Updated frontend help_interface to include setting up the display camera angle.
2015-11-14 Updated frontend so that the graphics now reflect whether the hardware derotator is derotating on startup or when QueryHardware is called by the user. Updated arduino BaseServer so that when the user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
2015-11-28 arduino_case: Modified front cover to have larger pushbutton holes so that the cover is easier to mount with pushbuttons. Mounting holes have been changed from hexagon holes to round. Side covers: He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
2016-01-01 controller.pdf: Added instructions for adding and LED light to the controller so that the pushbuttons can be seen in the dark.
2016-04-06 README.md: Added reference to Circuit Cellar Ink publication.
2016-04-26 README.md: Fixed Circuit Cellar Ink Issue numbers.

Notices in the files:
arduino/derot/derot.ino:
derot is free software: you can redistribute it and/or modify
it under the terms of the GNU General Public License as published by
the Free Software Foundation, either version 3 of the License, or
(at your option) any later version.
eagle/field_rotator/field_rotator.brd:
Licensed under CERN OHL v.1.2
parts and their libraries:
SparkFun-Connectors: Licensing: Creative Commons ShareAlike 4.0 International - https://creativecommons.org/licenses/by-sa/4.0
